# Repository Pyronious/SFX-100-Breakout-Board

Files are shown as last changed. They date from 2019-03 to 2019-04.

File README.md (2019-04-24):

# SFX-100-Breakout-Board
An Arduino Leonardo shield to simplify the wiring of SFX-100 serial port connectors

For more information about the SFX-100 project, please visit:
https://opensfx.com/

The "Group Buy Edition" is the latest and greatest.

The prototype works fine and uses the RJ45 connector for the E-stop instead of a screw terminal.

Releases
========
v1.35 April 24, 2019
A small modification to allow support for external power supplies higher than +5v. Not really necessary for our use case as powering by USB works fine and is typical for this application. But just in case someone out there does it differently for some reason. :)

========
v1.34 April 6, 2019
Group buy edition

This is the version of the board that was manufactured for the Group Buy.

* Replaced the modular jack with a screw terminal connector for simplicity and cost reduction.

* Removed JP1. You can shunt the screw terminal to test.

* DB25 connectors are now more symmetrical on the board for a cleaner design

* Board traces simplified and vias eliminated.

* Trace thickness increased

* Added additional holes for M3 mounting

* Updated enclosure

========
v1.32 March 23, 2019
Intial public release

J1 is a modular connector for running an Ethernet cable to your e-stop. You need to connect the wires from pins 1 and 8 to your e-stop switch.

If you are not using an e-stop, you must install a shunt jumper across JP1 to enable the circuit.

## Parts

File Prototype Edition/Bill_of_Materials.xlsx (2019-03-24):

Manufacturer Part Number | Manufacturer | Digi-Key Part Number | Customer Reference | Reference Designator | Packaging | Part Status | Quantity | Unit Price | Extended Price | Quantity Available | Mfg Std Lead Time | Description | RoHS Status | Lead Free Status | REACH Status | US Tariff Status
L77TSBH25SOL2RM8 | Amphenol ICC (Commercial Products) | L77TSBH25SOL2RM8-ND |  |  | Tray | Active | 4 | 1.84 | $7.36 | 83 | 6 Weeks | CONN D-SUB RCPT 25POS VERT SLDR | RoHS Compliant | Lead free | Not Available | Tariff Eligible
54602-908LF | Amphenol ICC (FCI) | 609-1046-ND |  |  | Bulk | Active | 1 | 0.6 | $0.60 | 73378 | 6 Weeks | CONN MOD JACK 8P8C R/A UNSHLD | RoHS Compliant | Lead free | Not Available
M20-9731045 | Harwin Inc. | 952-1841-ND |  |  | Bulk | Active | 1 | 0.47 | $0.47 | 1901 | 10 Weeks | CONN HEADER VERT 10POS 2.54MM | RoHS Compliant | Lead free | REACH Unaffected
M20-9730845 | Harwin Inc. | 952-1999-ND |  |  | Bulk | Active | 2 | 0.43 | $0.86 | 591 | 10 Weeks | CONN HEADER VERT 8POS 2.54MM | RoHS Compliant | Lead free | REACH Unaffected
M20-9730645 | Harwin Inc. | 952-1984-ND |  |  | Bulk | Active | 1 | 0.32 | $0.32 | 4896 | 10 Weeks | CONN HEADER VERT 6POS 2.54MM | RoHS Compliant | Lead free | REACH Unaffected
QPC02SXGN-RC | Sullins Connector Solutions | S9337-ND |  |  | Bag | Active | 1 | 0.1 | $0.10 | 750268 | 5 Weeks | CONN JUMPER SHORTING .100" GOLD | RoHS Compliant | Lead free | REACH Unaffected
M20-9730246 | Harwin Inc. | 952-3073-ND |  |  | Bulk | Active | 1 | 0.11 | $0.11 | 7276 | 10 Weeks | CONN HEADER VERT 2POS 2.54MM | RoHS Compliant | Lead free | REACH Unaffected

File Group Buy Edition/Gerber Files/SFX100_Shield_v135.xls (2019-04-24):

SFX100_Shield_v134 BOM
https://www.pcbcart.com/article/content/creating-a-bom.html | https://www.pcbcart.com/article/content/creating-a-bom.html | https://www.pcbcart.com/article/content/creating-a-bom.html | https://www.pcbcart.com/article/content/creating-a-bom.html | https://www.pcbcart.com/article/content/creating-a-bom.html | https://www.pcbcart.com/article/content/creating-a-bom.html | https://www.pcbcart.com/article/content/creating-a-bom.html | https://www.pcbcart.com/article/content/creating-a-bom.html
Manufacturer | Manufacturer Part Number (required) | Designator (required) | Qty (required) | Description (required) | SMD ,BGA,LCC,OR TH | Top/Bottom | Comment
Amphenol ICC (Commercial Products) | L77TSBH25SOL2RM8 | MOTOR1, MOTOR2, MOTOR3, MOTOR4 | 4 | CONN D-SUB RCPT 25POS VERT SLDR | TH | TOP | https://www.digikey.com/product-detail/en/amphenol-icc-commercial-products/L177TSBH25SOL2RM8/L177TSBH25SOL2RM8-ND/4884293
METZ CONNECT USA Inc. | 31055102.0000 | ESTOP | 1 | SCREW TYPE, TERMINAL BLOCK, RIGH | TH | TOP | https://www.digikey.com/product-detail/en/metz-connect-usa-inc/31055102/1849-1336-ND/9826615
Harwin Inc. | M20-9731045 | H1 | 1 | CONN HEADER VERT 10POS 2.54MM | TH | BOTTOM | https://www.digikey.com/product-detail/en/harwin-inc/M20-9731045/952-1841-ND/3727808
Harwin Inc. | M20-9730845 | H2, H3 | 2 | CONN HEADER VERT 8POS 2.54MM | TH | BOTTOM | https://www.digikey.com/product-detail/en/harwin-inc/M20-9730845/952-1999-ND/3727964
Harwin Inc. | M20-9730645 | H4 | 1 | CONN HEADER VERT 6POS 2.54MM | TH | BOTTOM | https://www.digikey.com/product-detail/en/harwin-inc/M20-9730645/952-1984-ND/3727949

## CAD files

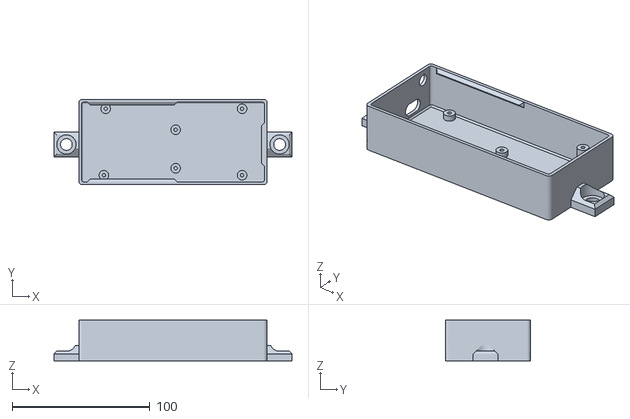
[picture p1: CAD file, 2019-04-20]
Group Buy Edition/Enclosure/SFX100_Shield_Box_M8_feet_v134.stl
172.8 x 61.9 x 29.6

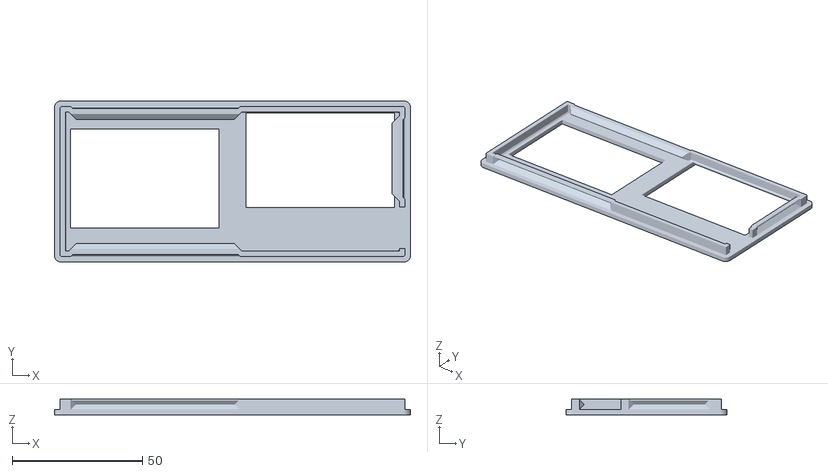
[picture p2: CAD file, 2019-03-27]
Prototype Edition/Enclosure/SFX100_breakout_box__lid_v132.stl
136.8 x 61.9 x 6.00

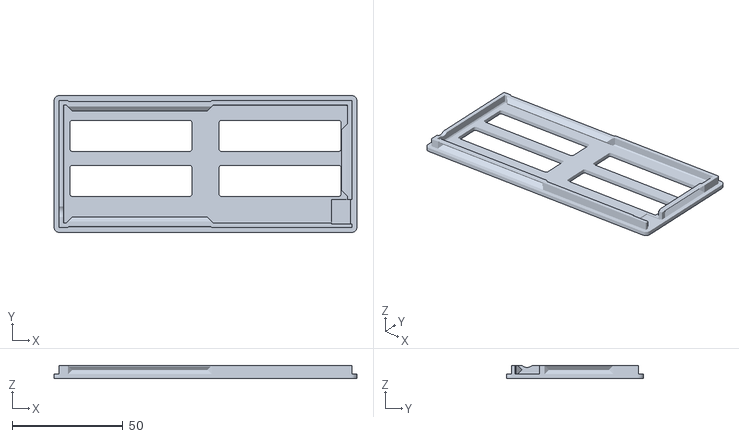
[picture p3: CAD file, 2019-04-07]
Group Buy Edition/Enclosure/SFX100_Shield_Lid_no_logo_v134.stl
136.8 x 61.9 x 6.00

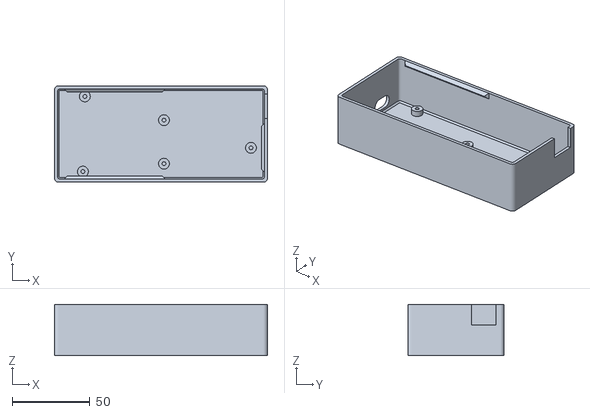
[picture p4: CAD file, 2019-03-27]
Prototype Edition/Enclosure/SFX100_breakout_box_v132.stl
136.8 x 61.9 x 33.0

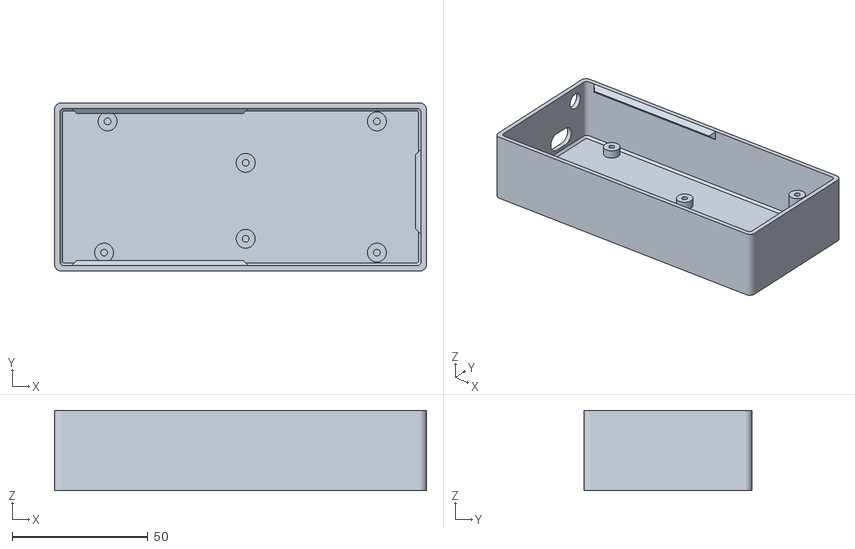
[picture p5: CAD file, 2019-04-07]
Group Buy Edition/Enclosure/SFX100_Shield_Box_no_feet_v134.stl
136.8 x 61.9 x 29.6

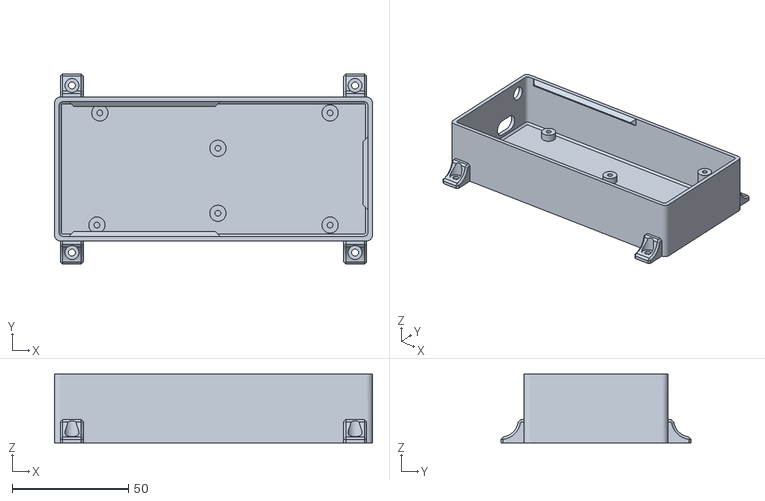
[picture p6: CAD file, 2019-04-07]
Group Buy Edition/Enclosure/SFX100_Shield_Box_with_feet_v134.stl
136.8 x 81.9 x 29.6

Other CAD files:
Group Buy Edition/Enclosure/SFX100_Shield_Lid__with_logo_v134.stl

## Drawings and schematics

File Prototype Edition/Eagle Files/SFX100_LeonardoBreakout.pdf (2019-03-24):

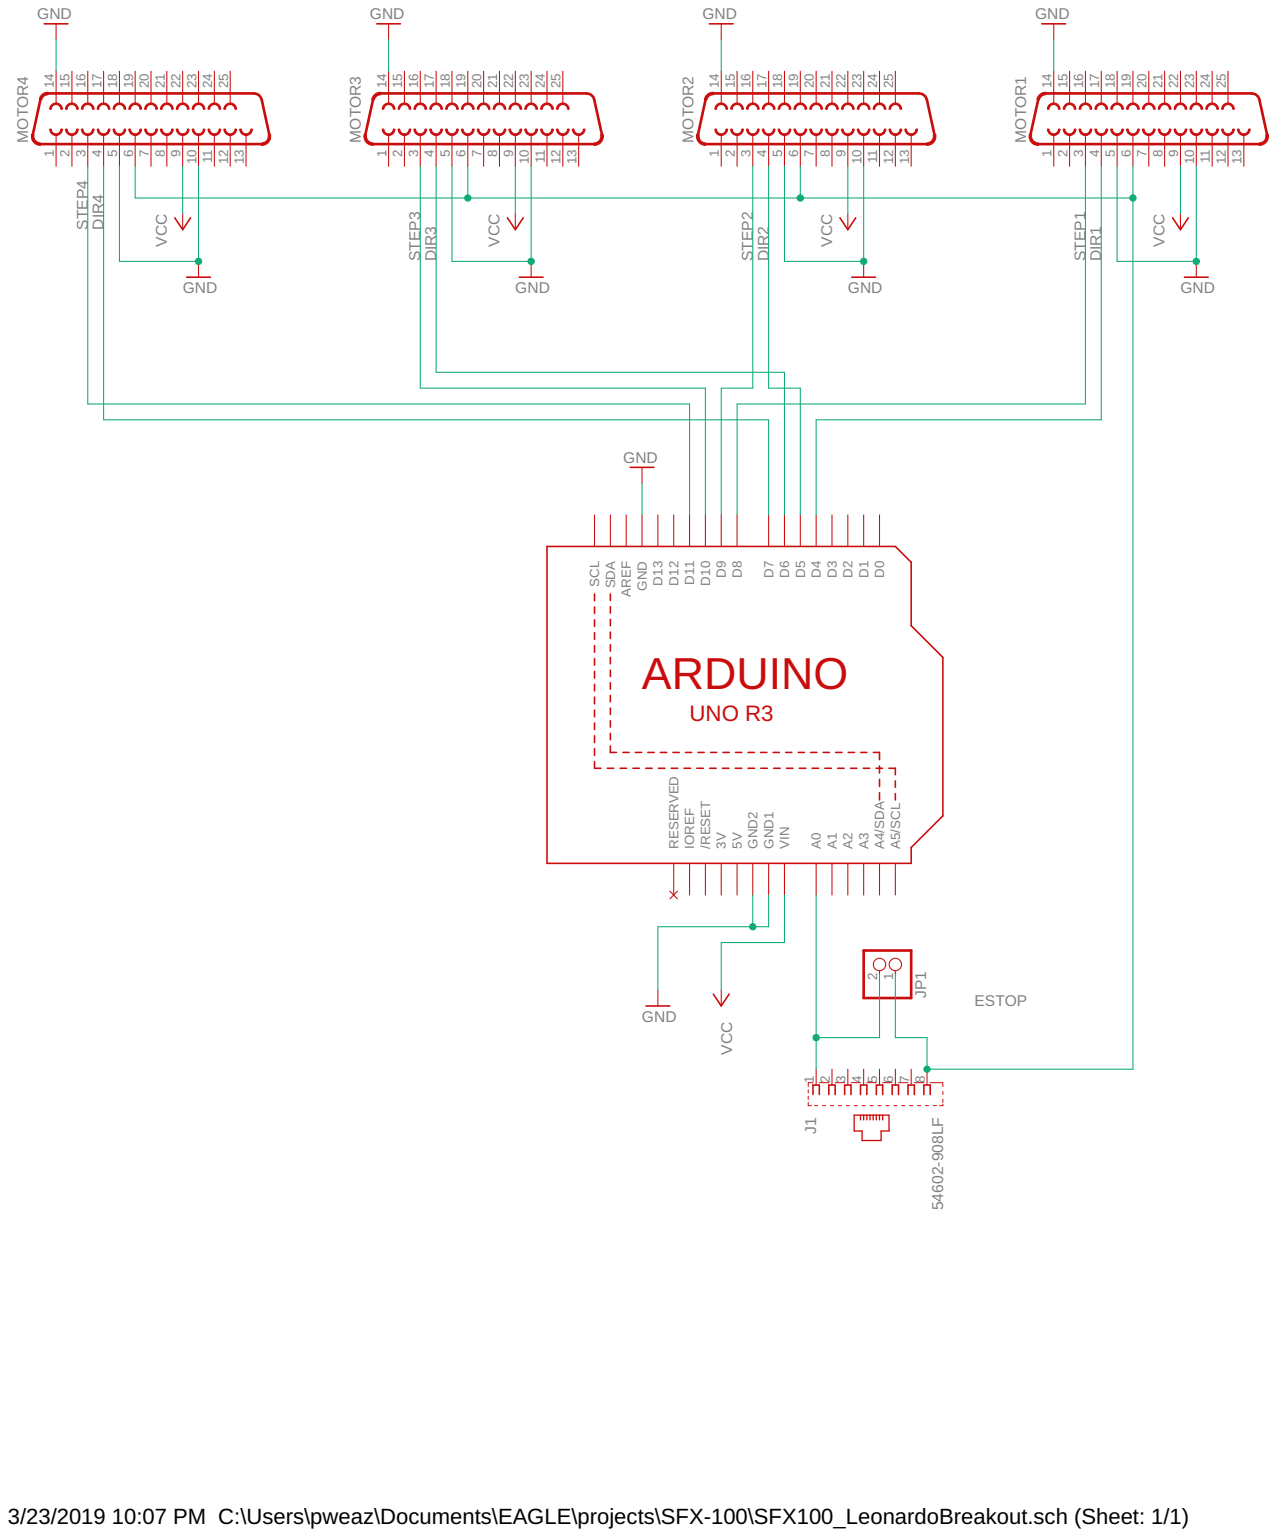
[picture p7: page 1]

3/23/2019 10:07 PM C:\Users\pweaz\Documents\EAGLE\projects\SFX-100\SFX100_LeonardoBreakout.sch (Sheet: 1/1)

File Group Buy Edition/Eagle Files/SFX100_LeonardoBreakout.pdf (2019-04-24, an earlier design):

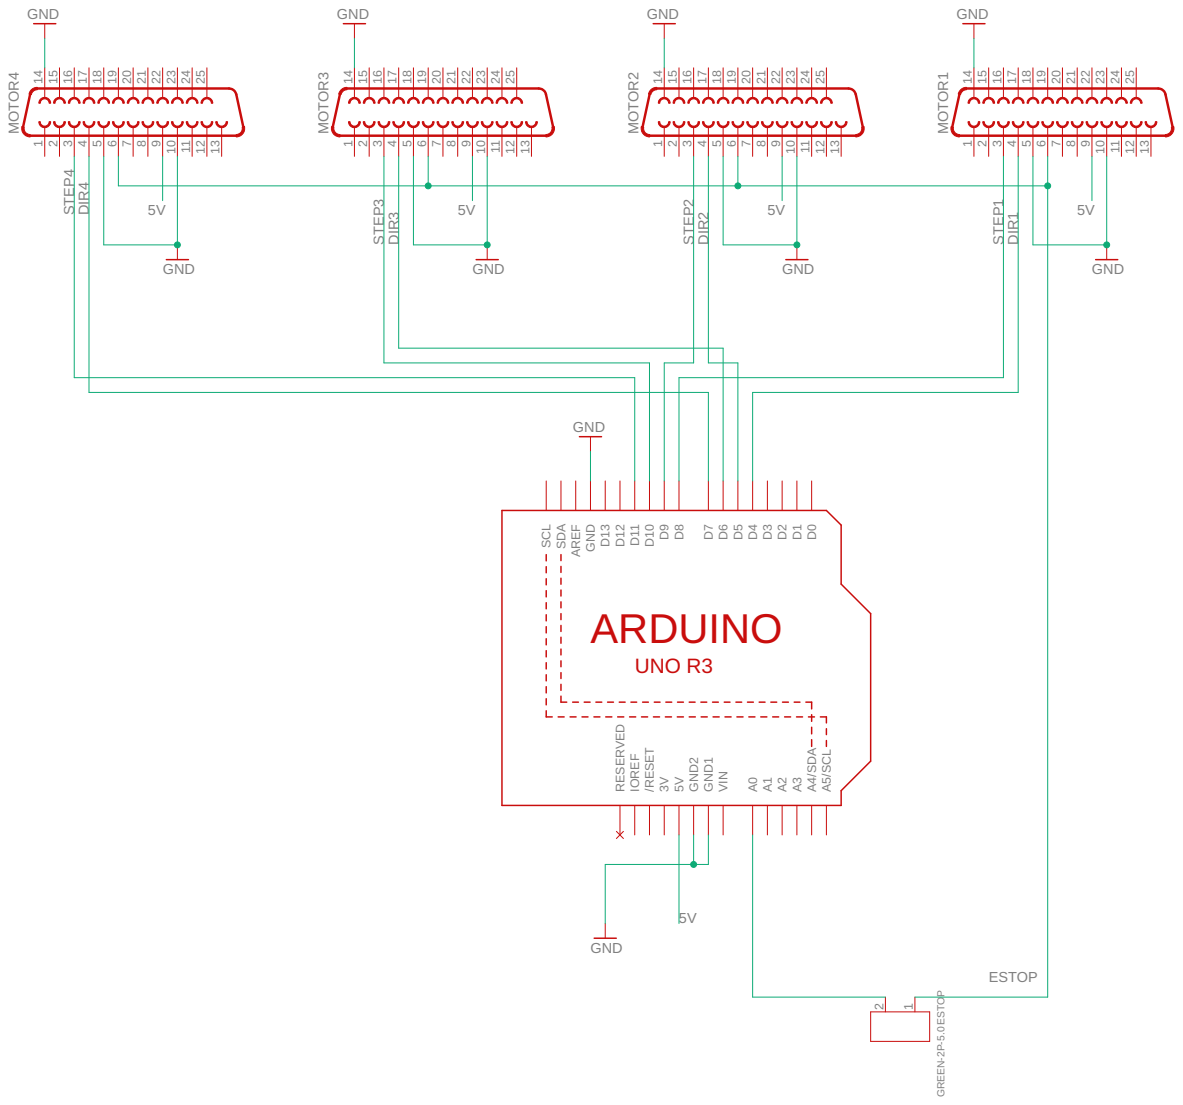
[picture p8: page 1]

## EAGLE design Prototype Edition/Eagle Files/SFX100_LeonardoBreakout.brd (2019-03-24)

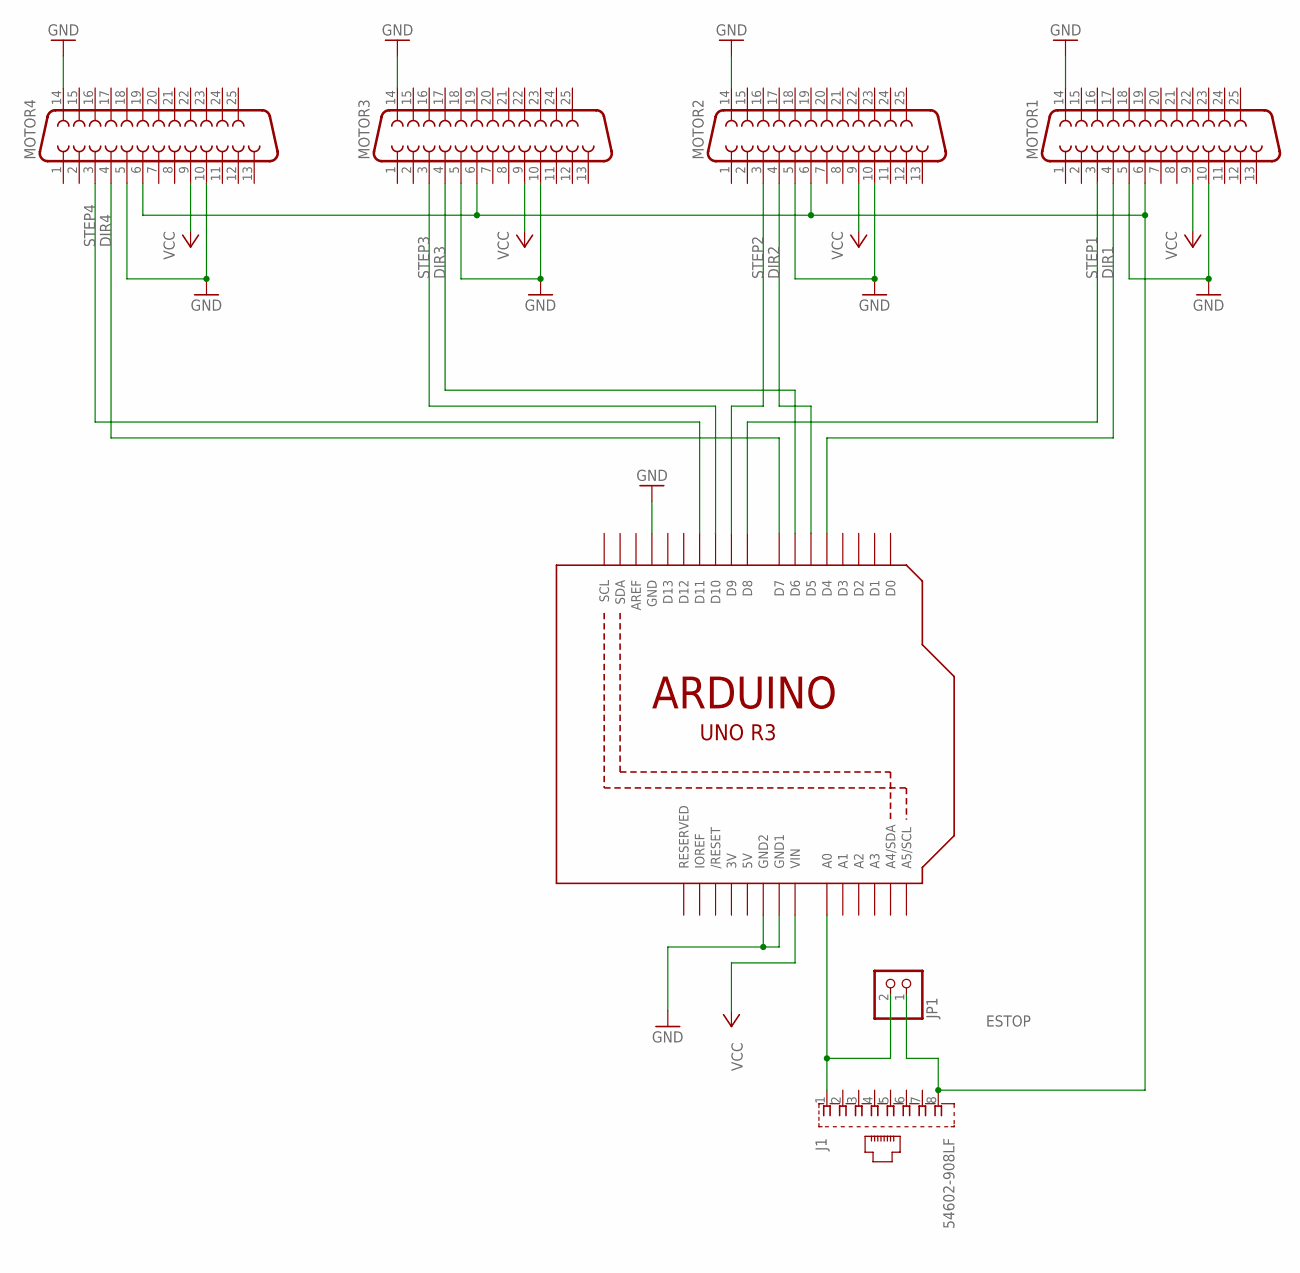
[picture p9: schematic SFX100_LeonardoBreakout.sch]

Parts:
J1: 54602-908LF; AMPHENOL_54602-908LF
JP1: PINHD-1X2; 1X02
MOTOR1, MOTOR2, MOTOR3, MOTOR4: F25V
U1: ARDUINOR3-BPLACE

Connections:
3V: U1.3V
5V: U1.5V
DIR1: MOTOR1.4, U1.D4
DIR2: MOTOR2.4, U1.D5
DIR3: MOTOR3.4, U1.D6
DIR4: MOTOR4.4, U1.D7
ENA: J1.1, JP1.2, U1.A0
ESTOP: J1.8, JP1.1, MOTOR1.6, MOTOR2.6, MOTOR3.6, MOTOR4.6
GND: MOTOR1.5, MOTOR1.10, MOTOR1.14, MOTOR2.5, MOTOR2.10, MOTOR2.14, MOTOR3.5, MOTOR3.10, MOTOR3.14, MOTOR4.5, MOTOR4.10, MOTOR4.14, U1.GND, U1.GND1, U1.GND2
STEP1: MOTOR1.3, U1.D8
STEP2: MOTOR2.3, U1.D9
STEP3: MOTOR3.3, U1.D10
STEP4: MOTOR4.3, U1.D11
VCC: MOTOR1.9, MOTOR2.9, MOTOR3.9, MOTOR4.9, U1.VIN

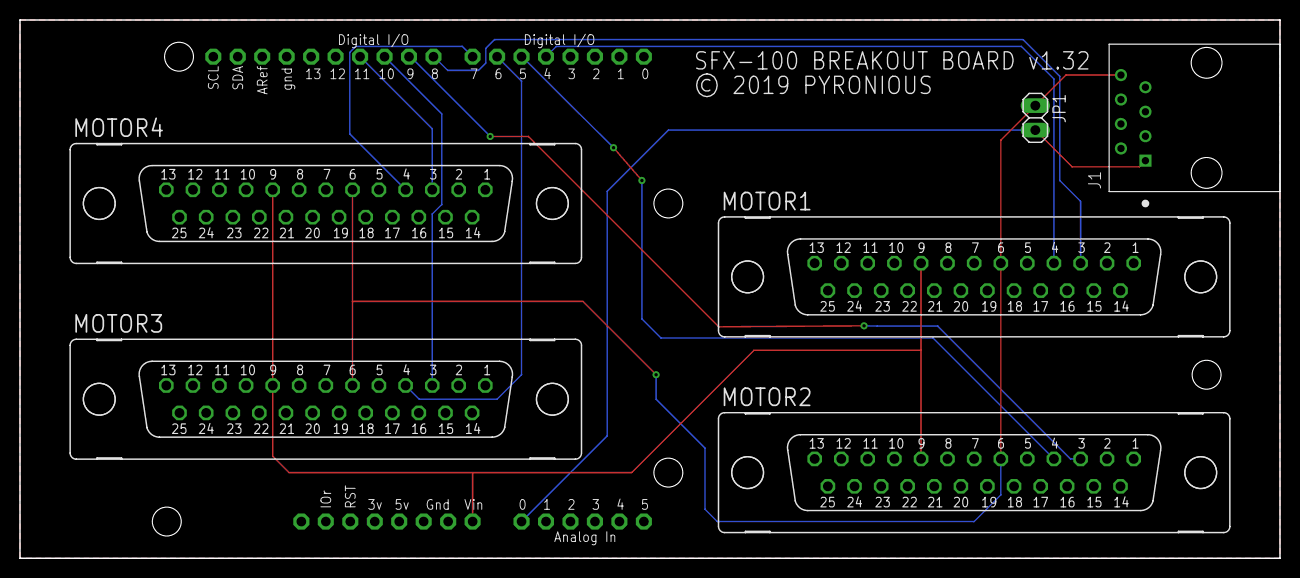
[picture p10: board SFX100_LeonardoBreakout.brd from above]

Board: 2 copper layers, 130.8 x 55.9 mm, 7 parts (0 on the bottom side), 12 nets.

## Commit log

2019-03-24 Initial Release
    Added initial public release of Gerber files, Eagle files, and bill of materials.
    [Bill_of_Materials.xlsx, SFX100_LeonardoBreakout.brd, SFX100_LeonardoBreakout.sch]
2019-03-27 Added 3D printable enclosure
    STL files now included for printing a box and lid.
    [SFX100_breakout_box.stl, SFX100_breakout_box__lid.stl]
2019-04-07 Updated to v1.34 "Group Buy" Edition
    v1.34 April 6, 2019
    Group buy edition
    This is the version of the board that was manufactured for the Group Buy.
    * Replaced the modular jack with a screw terminal connector for simplicity and cost reduction.
    * Removed JP1. You can shunt the screw terminal to test.
    * DB25 connectors are now more symmetrical on the board for a cleaner design
    * Board traces simplified and vias eliminated.
    * Trace thickness increased
    * Added additional holes for M3 mounting
    * Updated enclosure
    [Bill_of_Materials.xlsx, SFX100_LeonardoBreakout.brd, SFX100_LeonardoBreakout.sch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]
2019-04-20 Create SFX100_Shield_Box_M8_feet_v134.stl
    Added a new enclosure type with feet on the side for M8 socket cap screws.
    [SFX100_Shield_Box_M8_feet_v134.stl]
2019-04-24 Updated to final "group buy" design.
    [SFX100_LeonardoBreakout.brd, SFX100_LeonardoBreakout.sch, SFX100_Shield_Box_M8_feet_v134.stl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]
2019-04-24 Housekeeping update
    Renamed folders to "Group Buy Edition" and "Prototype Edition". Updated readme.
    [Bill_of_Materials.xlsx, SFX100_LeonardoBreakout.brd, SFX100_LeonardoBreakout.sch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]
2021-02-04 Create FUNDING.yml
    Added donation button. Thank you for your support!

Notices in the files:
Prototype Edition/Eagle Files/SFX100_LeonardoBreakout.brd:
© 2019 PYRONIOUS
